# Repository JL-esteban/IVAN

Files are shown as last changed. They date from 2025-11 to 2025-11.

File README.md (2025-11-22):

Proyecto hecho por las siguientes personas:
- Jose Esteban Lopez Montoya
- Alejandro Rodriguez Cortès
- Duberney Campo Tabares
- Felipe Ramirez Satizabal

En este github mostramos las conexiones, codigos tanto en arduino como en ros2, tambien simulación en RViz, que nos llevo a fformular este proyecto?, a quien no le gustaria controlar algo con solo el mover de sus manos?, que sea algo entretenido a la hora de sus terapias de recuperacion?, que las personas lo puedan usar tanto a la hora de su terapia como un juguete.

Así que comenzamos, tenemos de la siguiente fora su conexión y la cantidad de objetos,componentes,baterias y microchips que usamos.

Vamos a comenzar con el principal, la mano, la mano es aquella que va a ser de control con los movimientos de su muñeca, tu te preguntaras, como?, muy sencillo hay un modulo que se llama BMI160 el cual es un giroscopio y acelerometro, este modulo se programo para que soltara las coordenadas X Y, asi convertimos con el acelerometro que mande las posiciones como si fuera un mando,  no sabes que hace un mando?, te lo explico:

El mando tiene una serie de nombres los cuales las computadoras detectan como por ejemplo cada palanca, movimiento o boton por un axis, en nuestro caso es un R3 de un mando (es la palanca de la izquierda) esta palanca tiene dos axis los cuales son axis0 y axis1, el axis0 son los movimientos de izquierda y derecha, el axis1 son los movimientos de arriba y abajo, estos sueltan unos numeros los cuales el computador traduce para generar un movimiento a un personaje.

Teniendo eso en mente se supo que con las coordenadas de la mano y su giro podiamos hacer un joystick, el que lee eso es un Arduino UNO, el cual obtiene los datos y se los manda a el computador.

Ahora el computador con los datos del BMI160 ya como un joystick mandara la señal atravez de wifi al microchip del semisumergible que esta en el agua para poder moverse.

Ahora te explicare que tiene el semisumergible, que los autores de este repositorio lo llamaron como IVAN,IVAN tiene un ESP32, el cual resive los datos del computador atravez del wifi que son las direcciones dadas por el joystick(BMI160), este ESP32 le mandara la señal a un puente h, el cual es un tb6612fng, y este segun las direcciones dadas comenzara a mandar el voltaje a las salidas de A0 y A1 que son las salidas del primer motor y B0 B1 que son las salidas del segundo motor, todos los gnds de esta mismas estan conectadas entre ellas, y asi este se desplazaria por el agua.

No nos olvidemos de lo mas importante ¿conque alimentamos a IVAN?, IVAN tiene dos tipos de alimentación interna, una que es solo para el ESP32 y el otro el cual es solo para los motores, para alimentar el ESP32 se utilizaron 3 paquetes de pilas AA y esta salida de voltaje que dan 9V entran a un regulador de voltaje creado (que aqui se pasara la kicad) para que asi entren 9V y salgan 5V un buen voltaje con un buen amperaje que salen de las pilas para mantener prendido el ESP32 por un largo rato aproximadamente 30-40min, el tb6612fng  tiene dos pines uno llamado VCC y otro VM el VCC es aquel que resive entre 3.3V a 5V, los autores del proyecto alimentaron a 5V el tb6612fng y el VM a una bateria de 7.4V 1500mA

-------------------------------------------------------------------------------------------------------------------------------------------
EL CODIGO, LO IMPORTANTE QUE NECESITAS SABER
-------------------------------------------------------------------------------------------------------------------------------------------

  el que se llama Codigo_BMI160 es aquel codigo que conectaras el BMI160 con el ARDUINO UNO, a continuaciòn te explico como conectarlo:

  El BMI160 de la placa que yo te paso es realmente de 4 pines que es VCC,GND,SDA,SCL
, esos se pondran de la siguiente forma con el ARDUINO UNO, y es:
ESP32             |ARDUINO UNO
VCC --------------->5V
GND---------------->GND
SCL----------------->A5
SDA----------------->A4

con esas conexiones y el codigo de arduino que se otorgo te debe comenzar a mostrar coordenadas en la terminal.

Luego las conexiones de el ESP32 son de la siguiente forma:

Tb6612fng           |  ESP32
AIN1 ----------------> 25;
AIN2 ----------------> 26;
PWMA ----------------> 27;
BIN1 ----------------> 32;
BIN2 ----------------> 33;
PWMB ----------------> 14;
STBY ----------------> 12;

lo que es VM y VCC fue explicado anteriormente, y los puntos A0.A1.B0.B1 son los puntos de los motores A y B, que tipo de motores usamos?, usamos motores Hélice submarina cepillada BM70.

-----------------------------------------------------------------------------------------------------------------------------------------
una vez que has tenido esto vamos ha abrir el RVizte 
#iremos a la carpeta de ros2_ws
cd ~/ros2_ws

#cada vez que hagas un cambio o abras por primera vez una terminal en ubuntu debes poner el siguiente com  ando es ley  
colcon build --packages-select robot_boat

#cargamos el entorno
source install/setup.bash

#y ejecuta para verlo en rviz
ros2 launch robot_boat display.launch.py 

------------------------------------------------------------------------------------------------------------------------------------------
Ahora para cargar los codigos hay que hacerse de la siguiente manera
Vas al archivo de "AVANCE2" que esta en el principio del GitHub y abres dos terminales y ejecutas los siguientes comandos
# Terminal 1 - Lector BMI
source /opt/ros/humble/setup.bash
python3 lector_bmi160.py --ros-args -p serial_port:=/dev/ttyUSB0

# Terminal 2 - Control barco (después de que Terminal 1 funcione)
source /opt/ros/humble/setup.bash
python3 bmi_to_boat_control.py --ros-args -p esp32_ip:=192.168.4.1





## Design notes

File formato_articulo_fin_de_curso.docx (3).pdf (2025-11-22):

Avances sobre implementación de un robot acuático controlado por movimientos de la muñeca para la estimulación de la motricidad fina en Colombia. [MK06],

# Artículo de investigación como proyecto fin de curso

Research paper as a course end project

Alejandro Rodríguez Cortés
alejandro_rod@uao.edu.co
Duberney Campo Tabares
duberney.campo@uao.edu.co

Felipe Ramírez Satizabal
felipe.ramirez@uao.edu.co
José Esteban López
jose_esteban.lopez@uao.edu.co

Universidad Autónoma de Occidente, Facultad de Ingeniería, Programa de Ingeniería Mecatrónica (1) Universidad Autónoma de Occidente, Facultad de Ingeniería, Programa de Ingeniería Mecatrónica (2) Universidad Autónoma de Occidente, Facultad de Ingeniería, Programa de Ingeniería Mecatrónica (3) Universidad Autónoma de Occidente, Facultad de Ingeniería, Programa de Ingeniería Mecatrónica (4)

Resumen
Este informe presenta el análisis y búsqueda exhaustiva de fuentes de información para llevar a cabo nuestro proyecto de Robótica que está en búsqueda de la mejoría en el sector médico enfocándonos en el tema de la estimulación de la motricidad fina en Colombia.

La motricidad fina, y en particular la movilidad de la muñeca es determinante para el desarrollo de la autonomía funcional en la primera infancia e infancia, y para la recuperación de pacientes con limitaciones neurológicas y musculo esqueléticas. Sin embargo, los métodos tradicionales de estimulación y rehabilitación de la muñeca suelen apoyarse en ejercicios repetitivos y poco motivadores, lo que reduce la adherencia y limita el progreso de recuperación de la coordinación, fuerza y precisión.

La robótica ha demostrado ser un recurso innovador para estimular el movimiento y aumentar la participación de los usuarios. En este marco, el uso de un robot acuático controlado directamente por los movimientos de la muñeca representa una alternativa atractiva y novedosa. Con este enfoque, la persona no se sumergirá en el agua, en cambio manipulará al robot desde el exterior al mover la muñeca, el robot en este caso es un barco o objeto semisumergible que responde al movimiento de la muñeca desplazándose en el agua. Esta dinámica convierte la práctica en una experiencia lúdica y atractiva, que permite entrenar y evaluar la motricidad fina de la articulación.

En Colombia, pese a los avances en robótica educativa y en proyectos de rehabilitación, no se han implementado sistemas que integren la robótica acuática con el control directo a través de la muñeca. Esta ausencia tecnológica limita las posibilidades de contar con herramientas accesibles que integren la estimulación motora, la retroalimentación inmediata y la motivación lúdica. Como consecuencia, tanto niños en edad escolar como pacientes en procesos de rehabilitación continúan dependiendo principalmente de métodos tradicionales, los cuales, aunque han demostrado un grado de efectividad, no siempre garantizan un progreso sostenido ni permiten una evaluación objetiva del desempeño motor.

Palabras Clave: Motricidad fina, robótica, estimulación

Abstract
This report presents the analysis and exhaustive search for sources of information to carry out our Robotics project, which seeks to improve the medical sector by focusing on the stimulation of fine motor skills in Colombia.

Fine motor skills, and in particular wrist mobility, are crucial for the development of functional autonomy in early childhood and for the recovery of patients with neurological and musculoskeletal limitations. However, traditional methods of wrist stimulation and rehabilitation often rely on repetitive and unmotivating exercises, which reduce adherence and limit progress in recovering coordination, strength, and precision.

Autor 1, Autor 2...& Autor N. [(año)]

Robotics has proven to be an innovative resource for stimulating movement and increasing user participation. In this context, the use of an aquatic robot controlled directly by wrist movements represents an attractive and novel alternative. With this approach, the person will not be submerged in water, but will instead manipulate the robot from the outside by moving their wrist. In this case, the robot is a boat or semi-submersible object that responds to the movement of the wrist by moving through the water. This dynamic makes the practice a fun and engaging experience, allowing for the training and evaluation of fine motor skills in the joint.

In Colombia, despite advances in educational robotics and rehabilitation projects, no systems have been implemented that integrate aquatic robotics with direct control via the wrist. This technological gap limits the availability of accessible tools that integrate motor stimulation, immediate feedback, and playful motivation. As a result, both school-age children and patients undergoing rehabilitation continue to rely primarily on traditional methods, which, although they have proven to be effective to a certain degree, do not always guarantee sustained progress or allow for an objective assessment of motor performance.

Keywords: Fine motor skills, robotics, stimulation

### 1. INTRODUCCIÓN

En el siguiente documento vamos a abordar los temas relacionados con la motricidad fina, con un enfoque en la movilidad de la muñeca, teniendo en cuenta los métodos de rehabilitación actuales que son repetitivos y poco motivadores lo cual limita el progreso en la recuperación de coordinación, fuerza y precisión.
El cómo se pueden solucionar ciertos problemas de esta área y como desde la robótica vamos a aportar hacia esta misma, la cual tiene pocas investigaciones acerca del uso de robótica de forma directa en el paciente sin necesidad de que este arme algún tipo de robot. Sino que él sea el que controle el robot a través de los movimientos que necesite hacer en su terapia.
La robótica ha mostrado un gran potencial en este campo, al ofrecer experiencias más dinámicas y efectivas en la estimulación motora. Sin embargo, la mayoría de las investigaciones existentes se centran en sistemas complejos o de alto costo, sin explorar alternativas accesibles que integren la motivación lúdica con la terapia. En Colombia, no se han desarrollado propuestas que utilicen robótica acuática controlada directamente por la muñeca, lo que abre un espacio de innovación.
En este contexto, la presente investigación propone un enfoque novedoso en el que el paciente no construye el robot, sino que lo controla a través de los movimientos requeridos en su terapia. De esta manera, se busca integrar la estimulación motora, la retroalimentación inmediata y la motivación lúdica, aportando al estado actual de la ciencia y a la comprensión del problema desde una perspectiva terapéutica y educativa.

### 2. MATERIALES Y MÉTODOS/METODOLOGÍA

Diseño Conceptual y Selección de Componentes
Iniciaremos investigando los ejercicios de rehabilitación para identificar los movimientos clave de la muñeca que controlarán el vehículo. Con base en esto, se seleccionará el sensor y microcontrolador idóneos para capturar dichos movimientos, junto con los motores y propulsores adecuados para el entorno acuático. Finalmente, se elaborará una lista detallada de todos los componentes de hardware necesarios y las herramientas de software a utilizar.

Desarrollo del Hardware y Software
Se enfoca en la construcción física del prototipo, montando los motores y sellando la electrónica en una caja hermética, mientras que en paralelo se programará el firmware para traducir los datos del sensor inercial de la muñeca en comandos de control que transmitidos de forma inalámbrica gobiernen la velocidad y dirección de los motores del vehículo acuático. Se construirá el prototipo físico, montando los motores y sellando la electrónica. Paralelamente, se programará el firmware para traducir los datos del sensor inercial de la muñeca en comandos de control que se transmitirán de forma inalámbrica para gobernar la velocidad y dirección del vehículo.

Para el control del robot, se utilizará un sistema embebido con Linux para aprovechar su flexibilidad en la programación y el uso de librerías avanzadas. Esto facilitará la implementación de algoritmos de filtrado (como un Filtro de Kalman) para reducir el ruido del sensor, lo cual es crucial para abordar los riesgos de control y programación .
Para mitigar los riesgos de integración de sistemas , el desarrollo se hará de manera modular. Primero se validará el funcionamiento de cada componente por separado y luego se integrarán progresivamente para asegurar una comunicación y un control fluidos y precisos. Este enfoque minimiza los problemas de compatibilidad y comunicación entre los distintos subsistemas del robot.

Diagramas de conexion y simulaciones

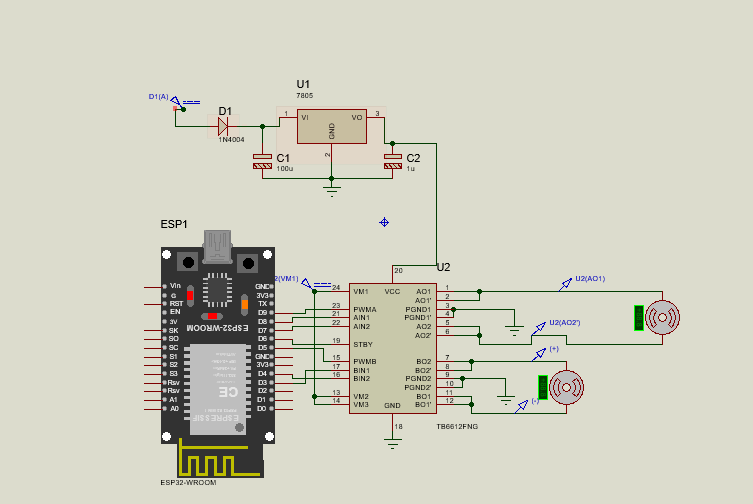
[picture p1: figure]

Imagen #1. Esquema interno de IVAN_Bote

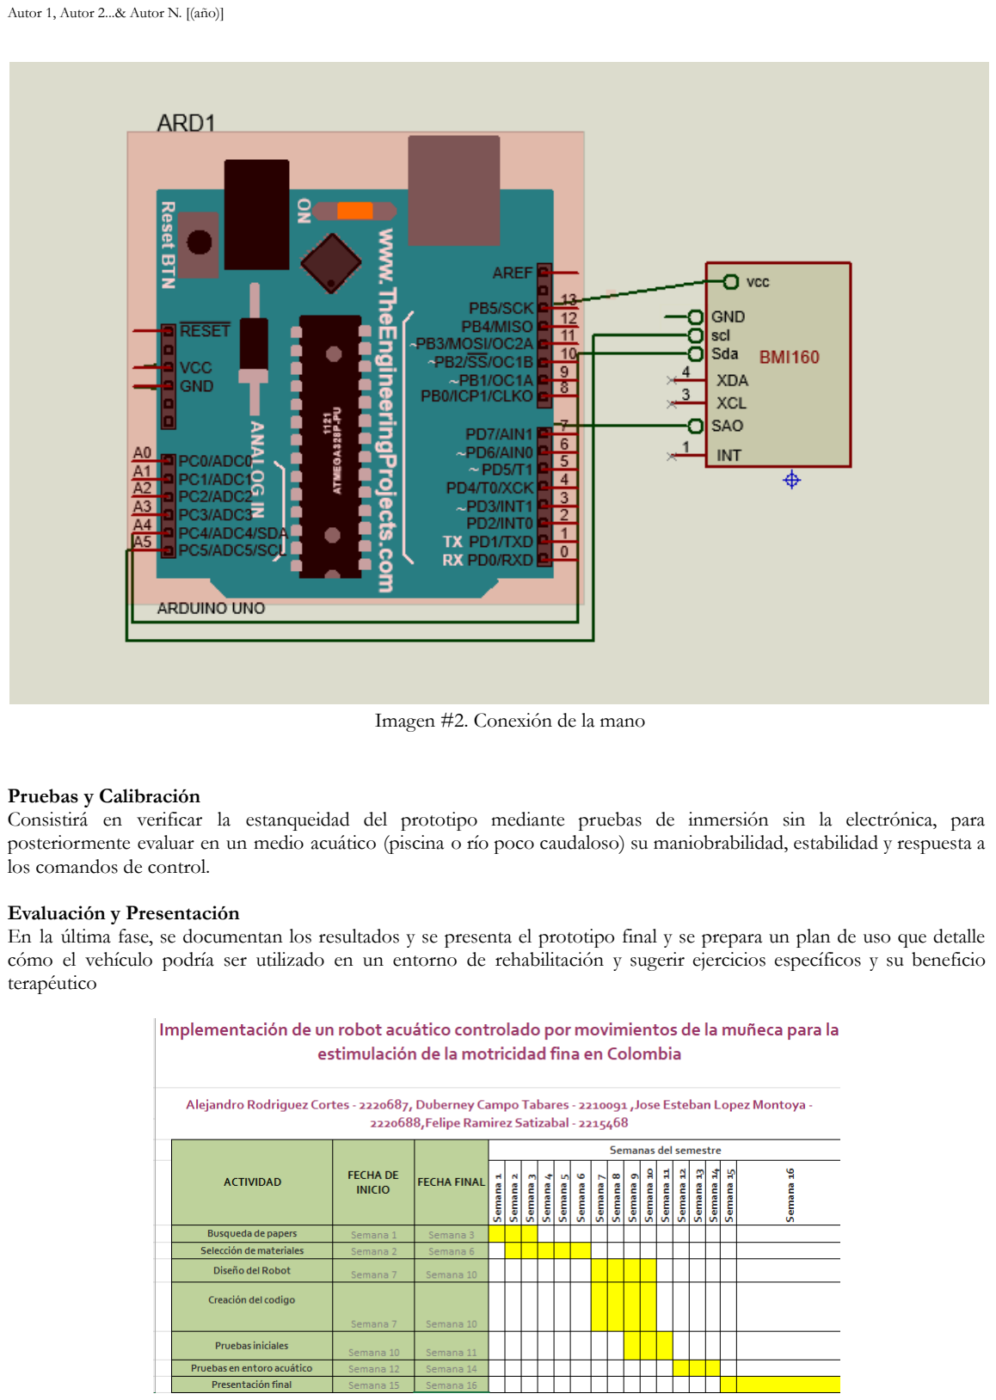
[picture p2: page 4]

Imagen #2. Conexión de la mano

Pruebas y Calibración
Consistirá en verificar la estanqueidad del prototipo mediante pruebas de inmersión sin la electrónica, para posteriormente evaluar en un medio acuático (piscina o río poco caudaloso) su maniobrabilidad, estabilidad y respuesta a los comandos de control.

Evaluación y Presentación
En la última fase, se documentan los resultados y se presenta el prototipo final y se prepara un plan de uso que detalle cómo el vehículo podría ser utilizado en un entorno de rehabilitación y sugerir ejercicios específicos y su beneficio terapéutico

Tabla #1. Elaboración propia

Tabla 1. Elaboración propia diagrama de gantt [8]

Se usará un microchip el cual con un sensor qué detecte el movimiento de la mano qué para ese tipo de casos un acelerómetro y giroscopio qué serian la mejor elección para esta tarea, se transmitirá una señal con un radio de 100m a la redonda y un receptor de la señal mandada, con una fuente de voltaje con 1500mAh y 11.1v, con un convertidor dc/dc se bajara el voltaje de 11.1v a 8.4v para un puente h y así poder alimentar los motores, se usarán unos botones para apagar tanto el mecanismo de la mano como el robot qué andará en el agua, se usara otro botón para qué el robot quede medio cuerpo sumergido utilizando el principio del submarino qué es absorber agua en un tanque haciendo qué se sumerja en el agua

Los componentes qué se va a usar en el proyecto son:

objeto | cantidad | dólar | peso colombiano | link de compra
Conector de cable de alambre rápido de 2A, 250 V, 2 pines, 3 pines | 20 | | $ 8.000 | averigua duberney
eBoot 20 AWG JST Cables y conectores para lámparas LED | 4 | | $ 8.000 | averigua duberney
bmi160 | 1 | | $ 22.990 | Bmi160 Acelerómetro Y Giroscopio 6dof Gybmi160 | Cuotas sin interés (https://articulo.mercadolibre.com.co/MCO-637322661-bmi160-acelerometro-y-giroscopio-6dof-gybmi160-_JM)
Batería Lipo Turnigy 1000mah 3s 20c | 1 | | $ 82.000 | Batería Lipo Turnigy 1000mah 3s 20c | Cuotas sin interés (https://articulo.mercadolibre.com.co/MCO-1559039399-bateria-lipo-turnigy-1000mah-3s-20c-_JM)
Teyleten Robot TB6612FNG Dual DC motor paso a paso módulo controlador 1.2A pico 3.2A | 1 | $ 7,81 | $ 31.445 | ENLACE (https://www.amazon.com/-/es/Teyleten-TB6612FNG-m%C3%B3dulo-controlador-paquete/dp/B08J3S6G2N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)
LEADTOPS Cable de extensión LED RGB de 100 pies | 10m | | $ 34.000 | Cable Rgb 4 Hilos Para Extensiones De Cinta Led X (https://articulo.mercadolibre.com.co/MCO-592184567-cable-rgb-4-hilos-para-extensiones-de-cinta-led-x-10-metros-_JM)

| | | | 10 Metros | Cuotas sin interés (https://articulo.mercadolibre.com.co/MCO-592184567-cable-rgb-4-hilos-para-extensiones-de-cinta-led-x-10-metros-_JM)
Qidoe 5 interruptores basculantes redondos impermeables | 1 | | $ 1.900 | averigua duberney
2S Lipo - Hélice submarina cepillada BM70 de 8.4 V 22 W, sellado, impermeable, para bricolaje, juguete, ROV | 2 | $ 16,98 | $ 68.367 | Enlace
Convertidor DC-dc XL4015 5a | 1 | | $ 18.500 | averigua duberney
módulo ASK 433 MHz 100 metros transmisor RF STX882 y antena receptor SRX882 | 1 | | $ 4.000
PETG | | | $ 85.000
Módulo ESP32-Cam-MB con cámara Ov2640 ESP de 32 Mb | 1 | | $ 44.6 90 | Módulo ESP32-Cam-M B con cámara Ov2640 ESP de 32 Mb | Cuotas sin interés (https://www.mercadolibre.com.co/modulo-esp32-cam-mb-con-camara-ov2640-esp-de-32-mb/p/MCO36063720)
| | COMPLETO | $ 408.892
por persona | $ 102.223 | dólar hoy | 4026,3
nombres | Dinero que dio | mercado libre | $ 138.260
Alejandro | $ 170.400 | Bateria | $ 84.000
Duberney | $ 208.800 | ALI EXPRESS | $ 16.000
Esteban | $ 161.000 | Amazon | $ 172.078
Felipe | $ 109.000 | Centro | $ 67.000 | Falta

IMPREVISTOS | $ 160.446 | total de web | $ 477.338
total de personas que dio plata | $ 649.200

Tabla #2. Componentes y presupuesto del proyecto

### 3. RESULTADOS Y DISCUSIÓN

El desarrollo de este proyecto inició con un análisis riguroso de literatura y la recopilación de diversas perspectivas orientadas a justificar la pertinencia de abordar la motricidad fina mediante herramientas robóticas. La revisión incluyó trabajos relacionados con parálisis cerebral, terapias motoras y tecnologías aplicadas a la rehabilitación, los cuales permitieron comprender la relevancia clínica y pedagógica del entrenamiento de la motricidad fina en población infantil [1]–[4]. Asimismo, investigaciones recientes sobre sistemas robóticos aplicados a procesos terapéuticos evidencian que las plataformas interactivas y los entornos asistidos por tecnología pueden mejorar significativamente la participación y el desempeño motor de los usuarios [5]–[9]. A partir de estas fuentes se identificó una problemática central: los ejercicios tradicionales de motricidad fina suelen ser repetitivos y poco motivadores, especialmente para niños con dificultades motoras, lo cual reduce la adherencia y la efectividad del tratamiento [6], [7]. Esta observación permitió establecer la necesidad de una alternativa innovadora que integrara estimulación, motivación y control motor mediante un dispositivo robótico accesible y atractivo.

Con base en este análisis se planteó la propuesta de desarrollar un robot acuático controlado mediante los movimientos de la muñeca, empleando un sensor inercial para captar los gestos del usuario y transferirlos directamente al desplazamiento del robot en el agua. La literatura relacionada con sistemas robóticos en contextos clínicos y de interacción háptica–visual brindó fundamentos sobre el uso de dispositivos lúdicos como herramienta terapéutica, así como sobre el impacto positivo de la interacción física y el feedback inmediato en la recuperación motora [5], [9], [10], [14].

Posteriormente se realizó una revisión de trabajos similares y de propuestas tecnológicas aplicadas a entornos acuáticos, lo que permitió comprender el estado del arte y definir una ruta de desarrollo adecuada [12], [13]. Con esta base se seleccionaron los componentes esenciales del sistema: motores impermeables para la movilidad en el agua, un sensor BMI160 para captar los movimientos de la muñeca y microcontroladores encargados del procesamiento y la comunicación. Aunque se emplearon otros elementos complementarios (reguladores, baterías y partes estructurales), estos componentes constituían la base funcional del sistema de control.

Inicialmente se contempló el uso de un sistema de transmisión radial para enviar desde un emisor en la muñeca las lecturas del BMI160 hacia un receptor ubicado en el robot. Sin embargo, durante las fases preliminares se identificaron limitaciones importantes en estabilidad y alcance de la señal, lo cual dificultaba su integración fluida durante la terapia. Este tipo de limitaciones en la comunicación es consistente con lo documentado en la literatura sobre diseño de robots móviles y procesos cooperativos entre dispositivos [11]. Debido a estos inconvenientes, se decidió migrar hacia un esquema más robusto basado en la conectividad WiFi del ESP32, mientras que el BMI160 se integró a un Arduino Uno para la captura de datos. Esta combinación permitió obtener un control más estable y una respuesta más suave, logrando que los movimientos de la muñeca se reflejaran de manera directa y precisa en el desplazamiento del robot.

El diseño físico del robot, su integración electrónica y las pruebas de funcionamiento representaron una de las etapas más enriquecedoras del proyecto. Controlar un robot acuático mediante los movimientos de la muñeca ofreció una experiencia particularmente innovadora, en contraste con los dispositivos tradicionales que emplean controles manuales convencionales. Además, el diseño buscó ser amigable y atractivo para niños con dificultades motoras, siguiendo recomendaciones de estudios previos que resaltan el valor del componente lúdico para mejorar la disposición del usuario en actividades terapéuticas [5]–[7]. Esta característica resultó fundamental: en las pruebas iniciales los usuarios manifestaban tal nivel de inmersión y disfrute que, en muchos casos, olvidaban que realizaban ejercicios de terapia, confirmando el potencial motivacional señalado en la literatura [6], [9], [14].

Durante el proceso de simulación se lograron avances importantes, aunque también se enfrentaron desafíos significativos. El entorno RViz permitió una visualización correcta del modelo y facilitó la comprensión espacial del robot dentro del entorno virtual. Sin embargo, en Gazebo se presentaron múltiples dificultades debido al alto peso computacional de los archivos STL, lo que provocaba bloqueos frecuentes y fallos completos del sistema. Este tipo de limitaciones es común en simulaciones complejas de robots con geometrías detalladas, especialmente cuando el hardware disponible es limitado [9], [13]. La única manera de obtener una simulación funcional fue reduciendo la geometría a modelos extremadamente simples, lo que se alejaba considerablemente del diseño real, pero aun así permitió validar conceptos fundamentales sobre optimización en ROS2.

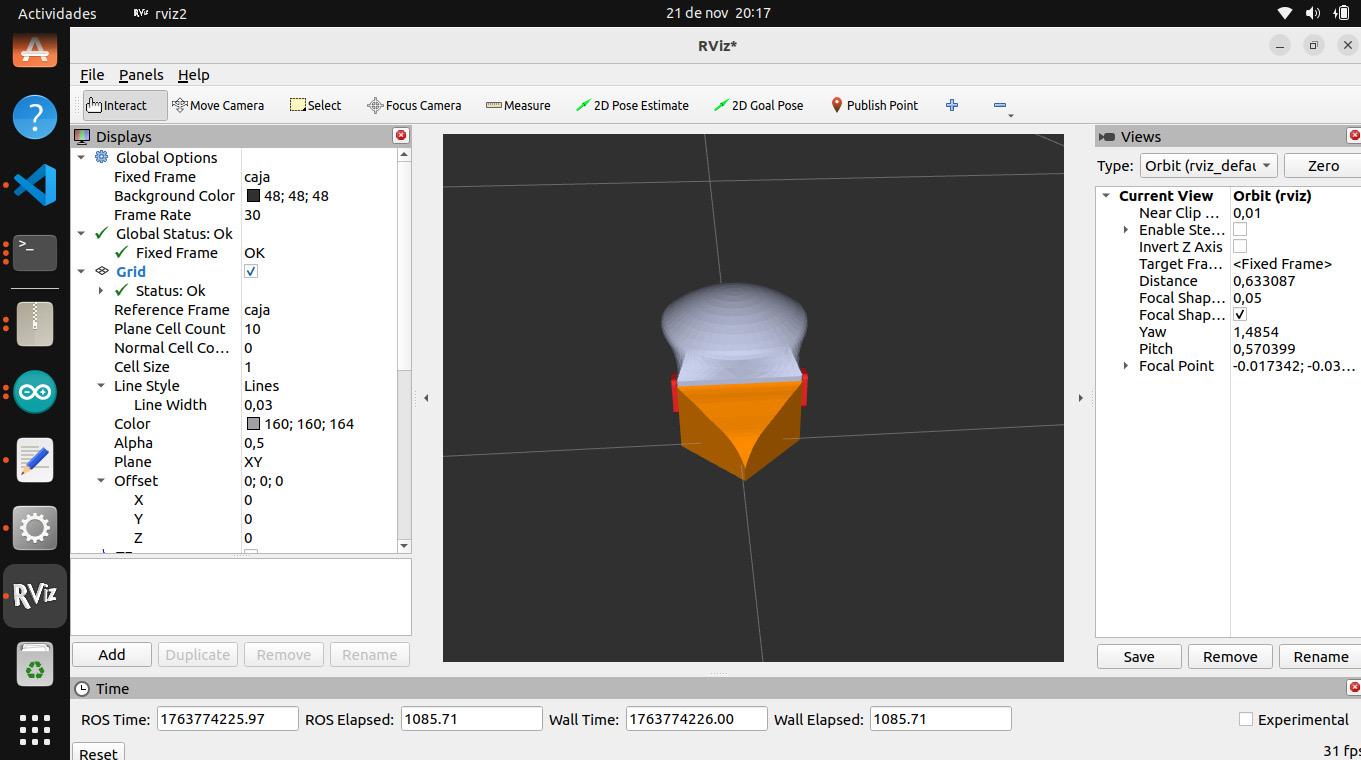
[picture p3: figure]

Imagen #3. Rviz de nuestro robo- elaboración propia

El uso de ROS2 representó un aprendizaje profundo, al requerir la instalación y manejo de un sistema operativo específico, la comprensión de la arquitectura basada en nodos y la integración de distintos paquetes para visualización, simulación y comunicación. Este proceso amplió de manera notable nuestra comprensión de la robótica moderna y de los ecosistemas distribuidos que sustentan el desarrollo de sistemas autónomos en la actualidad [9], [11], [14].

Finalmente, el proyecto resultó altamente enriquecedor desde los ámbitos técnico, terapéutico y humano. Su implementación a mayor escala podría transformar la manera en que se desarrollan las terapias de motricidad fina, aportando una herramienta innovadora, motivante y eficaz, coincidiendo con las tendencias descritas en la literatura sobre rehabilitación asistida por robots [5], [9], [10], [13]. El único inconveniente real durante la implementación física fue el consumo energético: las pilas alcalinas utilizadas para alimentar el ESP32 se descargaban rápidamente, reduciendo el tiempo de operación y exigiendo reemplazos frecuentes. Este aspecto constituye una oportunidad clara de mejora para futuras versiones, mediante el uso de baterías recargables de mayor capacidad o sistemas de gestión energética más eficientes. En conjunto, el proyecto demuestra cómo la robótica puede integrarse de forma creativa y funcional en procesos terapéuticos, ofreciendo experiencias más atractivas, inmersivas y efectivas para los usuarios [5]–[9], [14].

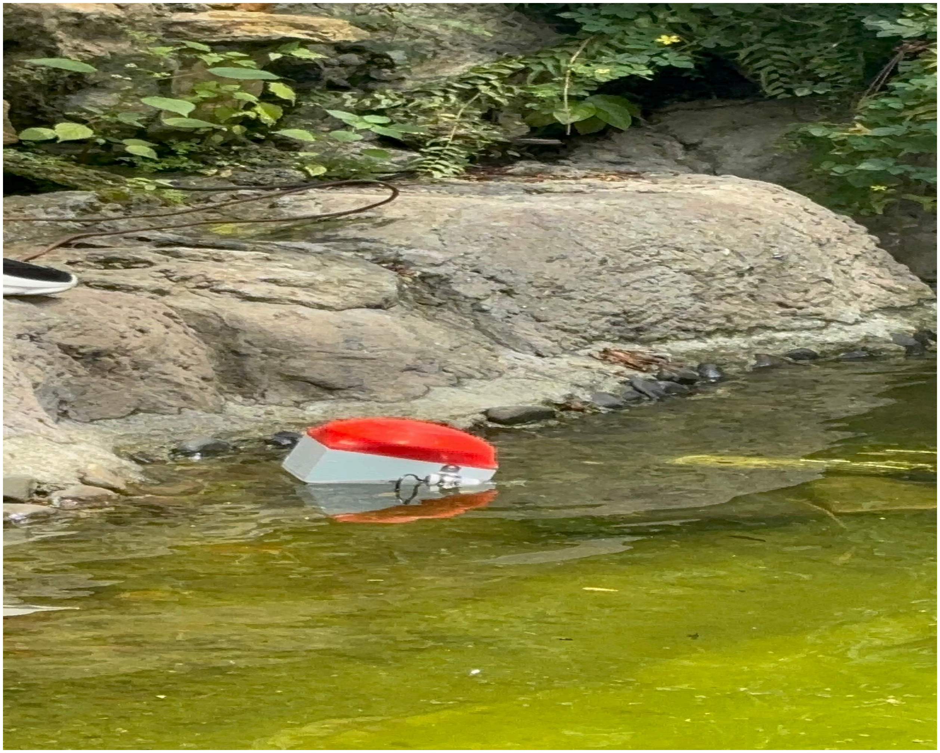
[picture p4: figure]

Imagen #4. IVAN en su primera prueba en el lago de la universidad

### 4. CONCLUSIONES

El proyecto demostró que la integración de tecnologías robóticas con enfoques terapéuticos puede mejorar significativamente los procesos de rehabilitación de la motricidad fina, especialmente en población infantil. A lo largo de su desarrollo se comprobó que el empleo de un robot acuático controlado mediante los movimientos de la muñeca no solo introduce un componente innovador, sino que también incrementa la motivación, la participación activa y la adherencia del usuario a las actividades terapéuticas. La combinación entre el sensor inercial, el control mediante ESP32 y el diseño amigable del robot permitió transformar ejercicios tradicionalmente repetitivos en experiencias lúdicas y dinámicas, lo cual constituye un aporte valioso para la fisioterapia y la rehabilitación motora.

En conjunto, los resultados del proyecto evidencian que la robótica, cuando se diseña con enfoque terapéutico y centrado en el usuario, puede convertirse en una herramienta altamente funcional, motivante y con potencial de impacto clínico. Esta iniciativa abre la puerta a nuevas investigaciones y mejoras, orientadas a robustecer el sistema, ampliar su autonomía y explorar otras aplicaciones en rehabilitación motora, posicionándose como un aporte significativo al campo de la tecnología para la salud.

REFERENCIAS

[1] S. Ccalla Auqui, Abordajes en parálisis cerebral infantil, Universidad Peruana Cayetano Heredia, 2023. [En
línea]. | Disponible | en:
https://repositorio.upch.edu.pe/bitstream/handle/20.500.12866/17241/Abordajes_CcallaAuqui_Sara.pdf?sequence=1
[2] D. Harghel Macari, Parálisis cerebral en el marco del máster universitario de fisioterapia en pediatría. Eficacia de la Terapia Acuática sobre la función motora gruesa en niños con Parálisis Cerebral con GMFCS I-IV , Trabajo Fin de Máster, Universidad Internacional de Valencia, 20210 https://eugdspace.eug.es/bitstream/handle/20.500.13002/821/Terapia%20Acu%c3%a1tica%20en%20Par%c3%a1lisis%20Cerebral.pdf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. (https://eugdspace.eug.es/bitstream/handle/20.500.13002/821/Terapia%20Acu%c3%a1tica%20en%20Par%c3%a1lisis%20Cerebral.pdf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)
[3] Recursos de Fisioterapia, “Escala de Función Motora Gruesa (GMFM) – Explicación completa y detallada.” Disponible en:
https://recursosfisioterapia.com/cuestionario-de-funcion-motora-gruesa-gmfm/
[4] CanChild, “GMFCS – E & R © 2007 CanChild Centre for Childhood Disability Research. Clasificación de la Función Motora Gruesa Extendida y Revisada. Disponible en: https://neuropediatoolkit.org/wp-content/uploads/2024/03/GMFCS-ER_Translation-Spanish.pdf
[5] A. L. Guerrero Hernández, Ó. A. Vivas Albán y J. M. Sabater Navarro, “Sistema de rehabilitación de motricidad fina de miembro superior utilizando juegos serios,” Ingeniería y Desarrollo, vol. 41, n.º 1, Universidad del Norte, 2023.
https://rcientificas.uninorte.edu.co/index.php/ingenieria/article/view/14894/214421446371
[6] Comunicación breve, “Escalas de motricidad fina,” Revista de Neurología Pediátrica, 2023. https://revistasanitariadeinvestigacion.com/escalas-de-motricidad-fina-comunicacion-breve/?utm_source=
[7] J. N. Orobio Aguiño y J. M. Montaño Rodriguez, Fortalecimiento de las habilidades motrices finas a través de actividades lúdicas en niños y niñas de 3 a 5 años del Hogar Comunitario La Fortaleza, Municipio de San Andrés de Tumaco (Nariño), Trabajo de grado (Profesional), Universidad Nacional Abierta y a Distancia (UNAD), 17 de abril de 2025.. Disponible en: https://repository.unad.edu.co/handle/10596/67947
[8] Elaboración propia agosto 29, 2025. Duberney Campo, Alejandro Rodriguez, Esteban Lopez y Felipe Ramirez.
[9] R. Llamas-Ramos, Robotic systems for the physiotherapy treatment of cerebral palsy, International Journal of Environmental Research and Public Health, vol. 19, no. 9, 2022. . Disponible en: https://www.mdpi.com/1660-4601/19/9/5116?utm_source
[10] B. R. Brewer, S. K. McDowell y L. C. Worthen-Chaudhari, “Poststroke upper extremity rehabilitation: a review of robotic systems and clinical results,” Topics in Stroke Rehabilitation, vol. 14, no. 6, pp. 22–44, 2007.. Disponible en: https://pubmed.ncbi.nlm.nih.gov/18174114/
[11] R. C. Arkin, T. Balch y E. Nitz, “Communication of Behavioral State in Multi-Agent Retrieval Tasks,” Proceedings of IEEE International Conference on Robotics and Automation, 1995. doi: 10.1109/ROBOT.1995.1511216. Disponible en: https://ieeexplore.ieee.org/abstract/document/1511216
[12] Y. Li, H. Zhao, X. Chen y J. Zhang, “Development of a Water Surface Cleaning Robot: Design, Implementation, and Experiment,” Applied Sciences, vol. 12, no. 18, p. 9131, 2022. . Disponible en: https://www.mdpi.com/2076-3417/12/18/9131
[13] H. H. Lee, Y. J. Kim y S. K. Park, “Design and Development of a Rehabilitation Robot for Ankle Motricity Training,” Machines, vol. 9, no. 11, p. 254, 2021. Disponible en: https://www.mdpi.com/2075-1702/9/11/254
[14] L. B. Cortés, “Desarrollo de un entorno virtual para la rehabilitación motriz basado en interacciones háptico-visuales”, Revista Iberoamericana de Automática e Informática Industrial, vol. 9, no. 4, pp. '–' (año), Universidad Politécnica de Valencia. [En línea]. Disponible: https://polipapers.upv.es/index.php/RIAI/article/view/9043/9714

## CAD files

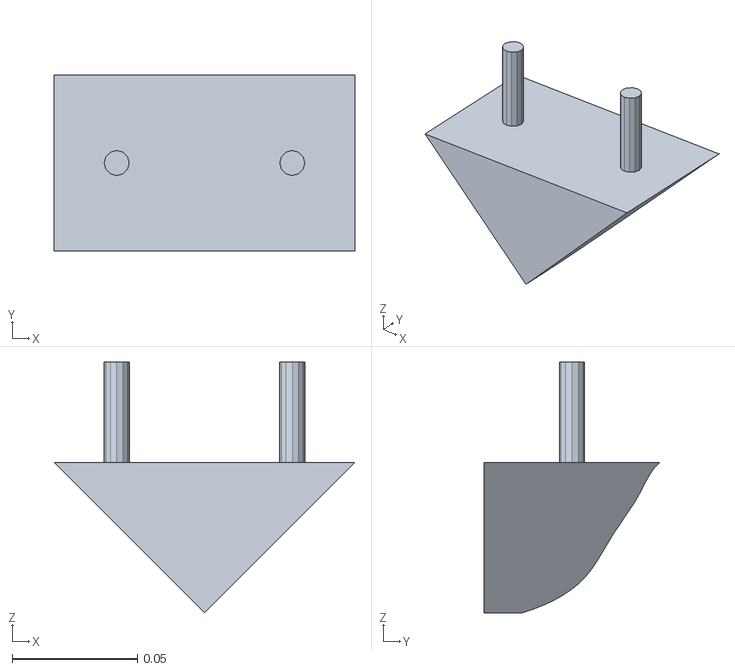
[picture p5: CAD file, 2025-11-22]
src/robot_boat/meshes/punta.STL
0.12 x 0.07 x 0.1

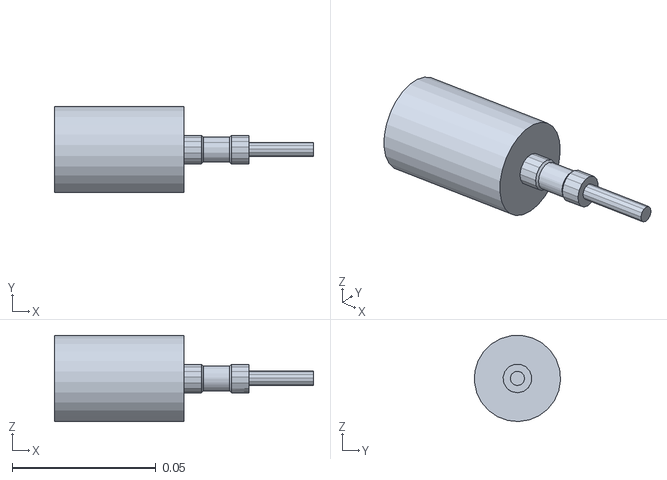
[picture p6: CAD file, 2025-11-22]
src/robot_boat_simple/robot_boat_simple/meshes/motor2.STL
0.09 x 0.0299 x 0.0299

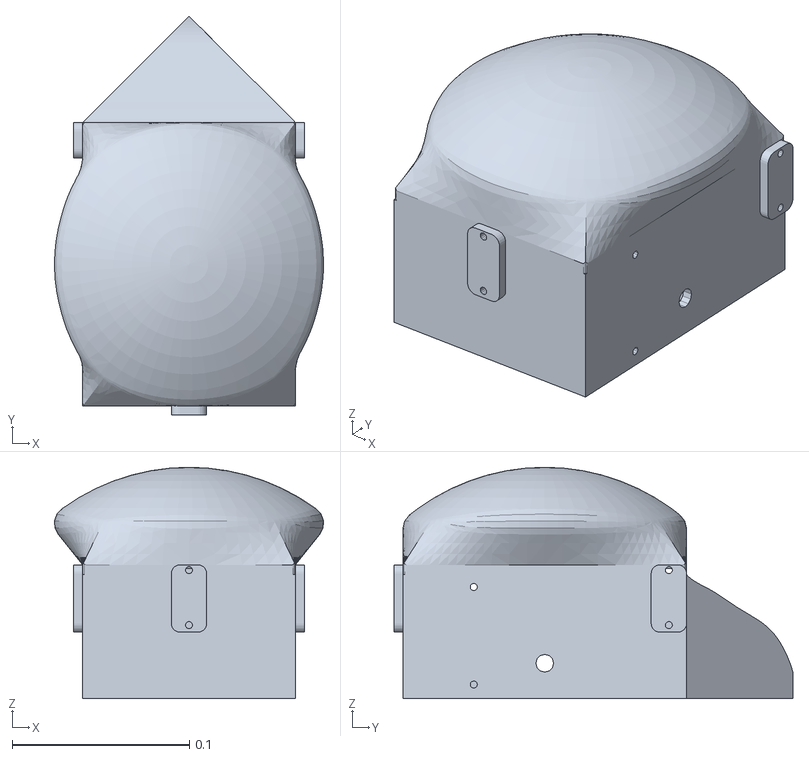
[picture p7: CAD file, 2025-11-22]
src/robot_boat_simple/robot_boat_simple/meshes/caja.STL
0.152 x 0.225 x 0.13

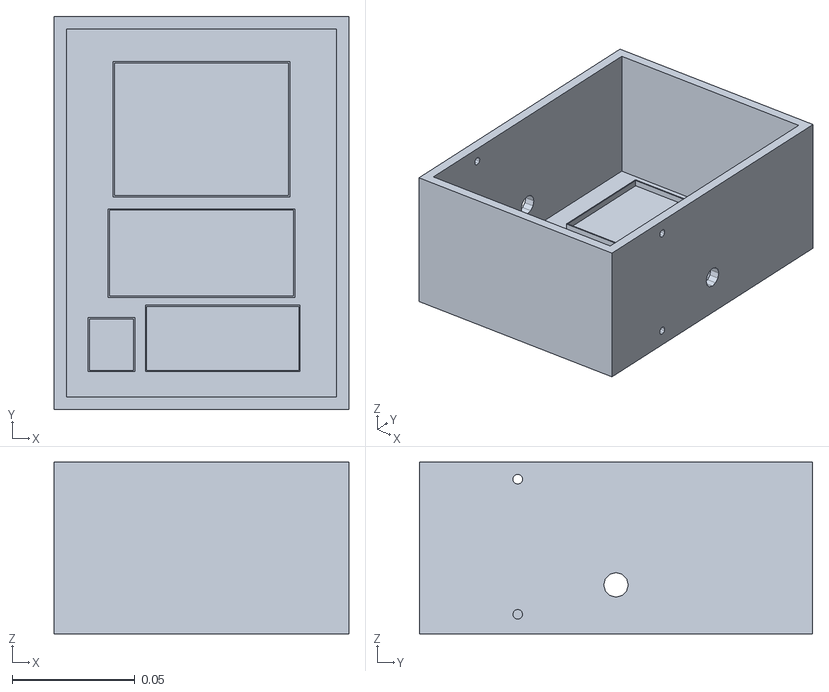
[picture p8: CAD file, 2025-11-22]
src/robot_boat/meshes/caja.STL
0.12 x 0.16 x 0.07

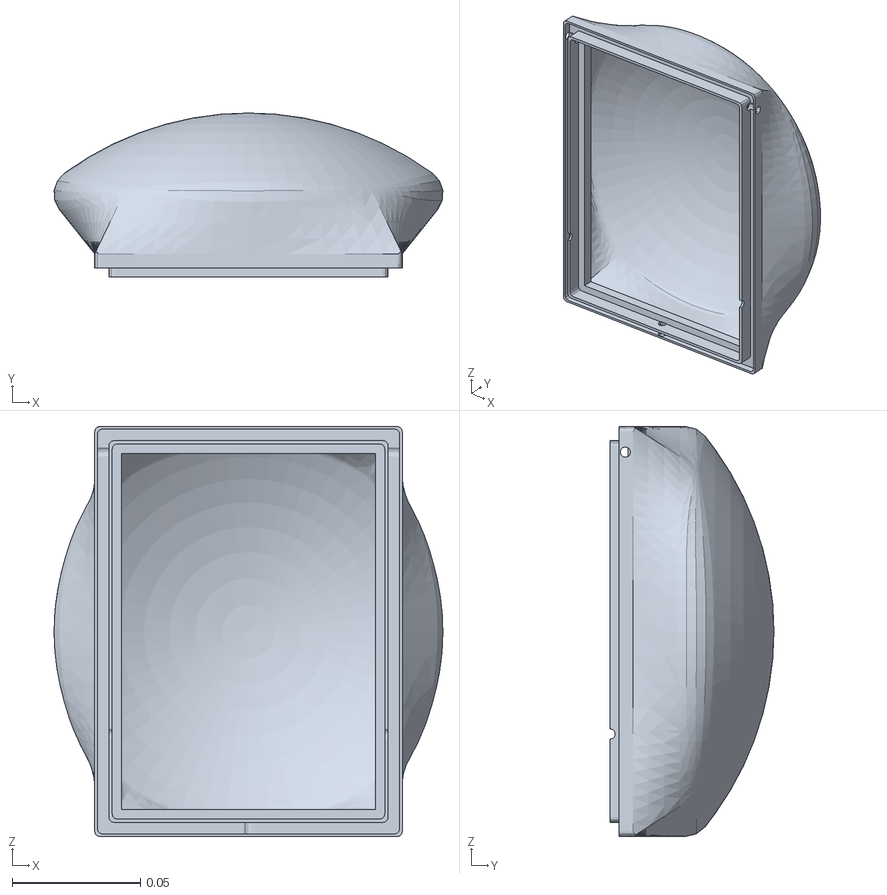
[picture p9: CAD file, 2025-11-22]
src/robot_boat/meshes/cabeza.STL
0.152 x 0.064 x 0.16

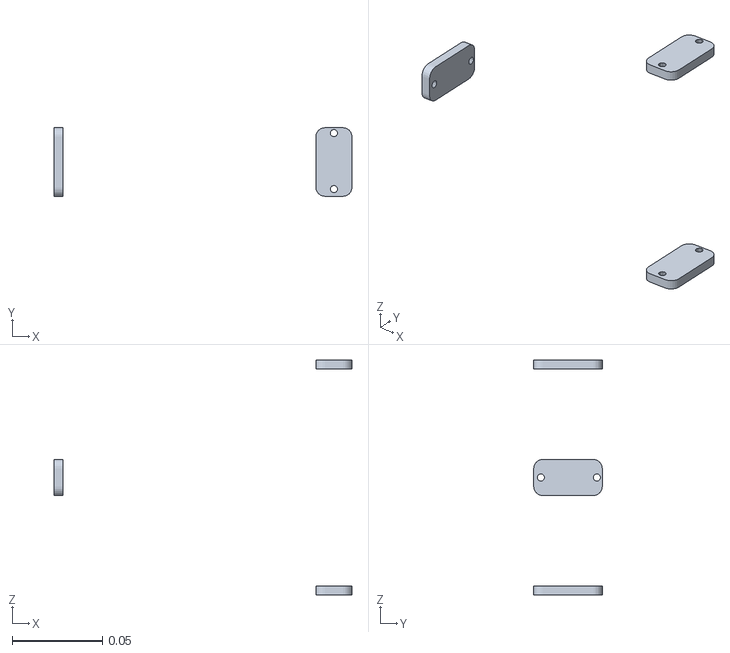
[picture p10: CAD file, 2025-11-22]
src/robot_boat/meshes/ganchos.STL
0.165 x 0.038 x 0.13

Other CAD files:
src/robot_boat/meshes/motor2.STL
src/robot_boat_simple/robot_boat_simple/meshes/motor1.STL
src/robot_boat/meshes/motor1.STL

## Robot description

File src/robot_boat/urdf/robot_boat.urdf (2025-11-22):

<?xml version="1.0" encoding="utf-8"?>
<robot name="robot_boat">

  <link name="caja">
    <inertial>
      <origin xyz="-0.00350655617226021 0.0057870557154398 0.100314646324909" rpy="0 0 0" />
      <mass value="0.315668074424316" />
      <inertia ixx="0.00106952247168509" ixy="-6.35663584540256E-08" ixz="4.48722793894617E-07" iyy="0.00147003359417461" iyz="1.732567854706E-06" izz="0.000700072373673693" />
    </inertial>
    <visual>
      <origin xyz="0 0 0" rpy="0 0 0" />
      <geometry>
        <mesh filename="package://robot_boat/meshes/caja.STL" />
      </geometry>
      <material name="azul_claro">
        <color rgba="0.792156862745098 0.819607843137255 0.933333333333333 1" />
      </material>
    </visual>
    <collision>
      <origin xyz="0 0 0" rpy="0 0 0" />
      <geometry>
        <mesh filename="package://robot_boat/meshes/caja.STL" />
      </geometry>
    </collision>
  </link>

  <link name="ganchos">
    <inertial>
      <origin xyz="-0.0508333333333334 -1.76145864720992E-05 -0.06" rpy="0 0 0" />
      <mass value="0.0107011061266654" />
      <inertia ixx="1.31036565577676E-06" ixy="1.52182167501141E-22" ixz="4.74293249589487E-24" iyy="3.76232518888044E-07" iyz="5.31604809467197E-23" izz="1.42091384800796E-06" />
    </inertial>
    <visual>
      <origin xyz="0 0 0" rpy="0 0 0" />
      <geometry>
        <mesh filename="package://robot_boat/meshes/ganchos.STL" />
      </geometry>
      <material name="rojo">
        <color rgba="1 0.168627450980392 0.168627450980392 1" />
      </material>
    </visual>
    <collision>
      <origin xyz="0 0 0" rpy="0 0 0" />
      <geometry>
        <mesh filename="package://robot_boat/meshes/ganchos.STL" />
      </geometry>
    </collision>
  </link>

  <joint name="ganchos" type="fixed">
    <origin xyz="0.056509 -0.03 0.039668" rpy="1.5708 0 1.5708" />
    <parent link="caja" />
    <child link="ganchos" />
    <axis xyz="0 0 0" />
  </joint>

  <link name="cabeza">
    <inertial>
      <origin xyz="-1.47210003906893E-05 0.0334212800408631 -1.71087868535286E-05" rpy="0 0 0" />
      <mass value="0.195566086436615" />
      <inertia ixx="0.000521416706885964" ixy="-3.28003379479109E-08" ixz="4.29670857435128E-08" iyy="0.000848517982242861" iyz="-6.74994053841756E-08" izz="0.000443795962264069" />
    </inertial>
    <visual>
      <origin xyz="0 0 0" rpy="0 0 0" />
      <geometry>
        <mesh filename="package://robot_boat/meshes/cabeza.STL" />
      </geometry>
      <material name="azul_claro">
        <color rgba="0.792156862745098 0.819607843137255 0.933333333333333 1" />
      </material>
    </visual>
    <collision>
      <origin xyz="0 0 0" rpy="0 0 0" />
      <geometry>
        <mesh filename="package://robot_boat/meshes/cabeza.STL" />
      </geometry>
    </collision>
  </link>

  <joint name="cabeza" type="fixed">
    <origin xyz="-0.07 0.01 -0.06" rpy="0 1.5707963267949 0" />
    <parent link="ganchos" />
    <child link="cabeza" />
    <axis xyz="0 0 0" />
  </joint>

  <link name="punta">
    <inertial>
      <origin xyz="3.27284758360044E-06 -0.00433760804571402 0.0273160015482659" rpy="0 0 0" />
      <mass value="0.0716405181094412" />
      <inertia ixx="5.44743781091978E-05" ixy="1.86774753169867E-09" ixz="6.76801340593279E-09" iyy="9.58237376978415E-05" iyz="-6.17934926455551E-06" izz="0.000101029420324114" />
    </inertial>
    <visual>
      <origin xyz="0 0 0" rpy="0 0 0" />
      <geometry>
        <mesh filename="package://robot_boat/meshes/punta.STL" />
      </geometry>
      <material name="naranja">
        <color rgba="1 0.549019607843137 0 1" />
      </material>
    </visual>
    <collision>
      <origin xyz="0 0 0" rpy="0 0 0" />
      <geometry>
        <mesh filename="package://robot_boat/meshes/punta.STL" />
      </geometry>
    </collision>
  </link>

  <joint name="punta" type="fixed">
    <origin xyz="-0.0034915 0.02 0.018168" rpy="1.5708 0 0" />
    <parent link="caja" />
    <child link="punta" />
    <axis xyz="0 0 0" />
  </joint>


  <link name="motor1">
    <inertial>
      <origin xyz="0.0248078639783107 0 0" rpy="0 0 0" />
      <mass value="0.0338272475621472" />
      <inertia ixx="3.59775886940148E-06" ixy="-8.70714672756417E-24" ixz="-9.65307491393635E-22" iyy="1.02720341448678E-05" iyz="0" izz="1.02720341448678E-05" />
    </inertial>
    <visual>
      <origin xyz="0 0 0" rpy="0 0 0" />
      <geometry>
        <mesh filename="package://robot_boat/meshes/motor1.STL" />
      </geometry>
      <material name="gris_claro">
        <color rgba="0.796078431372549 0.823529411764706 0.937254901960784 1" />
      </material>
    </visual>
    <collision>
      <origin xyz="90 0 0" rpy="0 0 0" />
      <geometry>
        <mesh filename="package://robot_boat/meshes/motor1.STL" />
      </geometry>
    </collision>
  </link>

  <joint name="motor1" type="continuous">
    <origin xyz="-0.04 -0.12 0.02" rpy="0 1.5708 0" />
    <parent link="caja" />
    <child link="motor1" />
    <axis xyz="1 0 0" />
    <limit effort="10.0" velocity="10.0" />
    <dynamics damping="0.1" friction="0.05" />
  </joint>


  <link name="motor2">
    <inertial>
      <origin xyz="0.0248078639783108 -6.93889390390723E-18 0" rpy="0 0 0" />
      <mass value="0.0338272475621472" />
      <inertia ixx="3.59775886940148E-06" ixy="3.03672443546408E-22" ixz="-1.21326837735656E-21" iyy="1.02720341448678E-05" iyz="0" izz="1.02720341448678E-05" />
    </inertial>
    <visual>
      <origin xyz="0 0 0" rpy="0 0 0" />
      <geometry>
        <mesh filename="package://robot_boat/meshes/motor2.STL" />
      </geometry>
      <material name="gris_claro">
        <color rgba="0.796078431372549 0.823529411764706 0.937254901960784 1" />
      </material>
    </visual>
    <collision>
      <origin xyz="0 0 0" rpy="0 0 0" />
      <geometry>
        <mesh filename="package://robot_boat/meshes/motor2.STL" />
      </geometry>
    </collision>
  </link>

  <joint name="motor2" type="continuous">
    <origin xyz="0.04 -0.12 0.02" rpy="0 1.5708 0" />
    <parent link="caja" />
    <child link="motor2" />
    <axis xyz="1 0 0" />
    <limit effort="10.0" velocity="10.0" />
    <dynamics damping="0.1" friction="0.05" />
  </joint>

  <gazebo reference="caja">
    <material>Gazebo/Blue</material>
    <kp>1000000.0</kp>
    <kd>100.0</kd>
  </gazebo>
  
  <gazebo reference="ganchos">
    <material>Gazebo/Red</material>
    <kp>1000000.0</kp>
    <kd>100.0</kd>
  </gazebo>
  
  <gazebo reference="cabeza">
    <material>Gazebo/Blue</material>
    <kp>1000000.0</kp>
    <kd>100.0</kd>
  </gazebo>
  
  <gazebo reference="punta">
    <material>Gazebo/Orange</material>
    <kp>1000000.0</kp>
    <kd>100.0</kd>
  </gazebo>
  
  <gazebo reference="motor1">
    <material>Gazebo/Grey</material>
    <kp>1000000.0</kp>
    <kd>100.0</kd>
  </gazebo>
  
  <gazebo reference="motor2">
    <material>Gazebo/Grey</material>
    <kp>1000000.0</kp>
    <kd>100.0</kd>
  </gazebo>

  <!-- Gazebo plugins -->
  <gazebo>
    <plugin name="gazebo_ros_control" filename="libgazebo_ros_control.so">
      <robot_namespace>/</robot_namespace>
    </plugin>
  </gazebo>

</robot>

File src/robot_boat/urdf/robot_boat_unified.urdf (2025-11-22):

<robot name="robot_boat">
  
  <!-- CUERPO PRINCIPAL (usando el STL de la caja) -->
  <link name="base">
    <inertial>
      <origin xyz="0 0 0.025" rpy="0 0 0" />
      <mass value="0.4" />
      <inertia ixx="0.001" ixy="0" ixz="0" iyy="0.001" iyz="0" izz="0.001" />
    </inertial>
    <visual>
      <geometry>
        <mesh filename="package://robot_boat/meshes/caja.STL"/>
      </geometry>
      <material name="azul_claro">
        <color rgba="0.792156862745098 0.819607843137255 0.933333333333333 1"/>
      </material>
    </visual>
    <collision>
      <geometry>
        <box size="0.15 0.1 0.05"/>
      </geometry>
    </collision>
  </link>

  <!-- PUNTA DELANTERA (cono naranja) -->
  <link name="punta">
    <inertial>
      <origin xyz="0 0 0" rpy="0 0 0" />
      <mass value="0.05" />
      <inertia ixx="0.0001" ixy="0" ixz="0" iyy="0.0001" iyz="0" izz="0.0001" />
    </inertial>
    <visual>
      <geometry>
        <cylinder length="0.05" radius="0.03"/>
      </geometry>
      <material name="naranja">
        <color rgba="1 0.549019607843137 0 1"/>
      </material>
    </visual>
    <collision>
      <geometry>
        <cylinder length="0.05" radius="0.03"/>
      </geometry>
    </collision>
  </link>

  <joint name="punta_joint" type="fixed">
    <origin xyz="0.08 0 0" rpy="0 0 0" />
    <parent link="base"/>
    <child link="punta"/>
  </joint>

  <!-- MOTOR IZQUIERDO -->
  <link name="motor_left">
    <inertial>
      <origin xyz="0 0 0" rpy="0 0 0" />
      <mass value="0.05" />
      <inertia ixx="0.0001" ixy="0" ixz="0" iyy="0.0001" iyz="0" izz="0.0001" />
    </inertial>
    <visual>
      <geometry>
        <cylinder length="0.08" radius="0.015"/>
      </geometry>
      <material name="gris_claro">
        <color rgba="0.796078431372549 0.823529411764706 0.937254901960784 1"/>
      </material>
    </visual>
    <collision>
      <geometry>
        <cylinder length="0.08" radius="0.015"/>
      </geometry>
    </collision>
  </link>

  <joint name="motor_left_joint" type="continuous">
    <origin xyz="-0.04 -0.08 0" rpy="0 1.5708 0" />
    <parent link="base"/>
    <child link="motor_left"/>
    <axis xyz="1 0 0"/>
    <limit effort="10.0" velocity="10.0"/>
    <dynamics damping="0.1" friction="0.05"/>
  </joint>

  <!-- MOTOR DERECHO -->
  <link name="motor_right">
    <inertial>
      <origin xyz="0 0 0" rpy="0 0 0" />
      <mass value="0.05" />
      <inertia ixx="0.0001" ixy="0" ixz="0" iyy="0.0001" iyz="0" izz="0.0001" />
    </inertial>
    <visual>
      <geometry>
        <cylinder length="0.08" radius="0.015"/>
      </geometry>
      <material name="gris_claro">
        <color rgba="0.796078431372549 0.823529411764706 0.937254901960784 1"/>
      </material>
    </visual>
    <collision>
      <geometry>
        <cylinder length="0.08" radius="0.015"/>
      </geometry>
    </collision>
  </link>

  <joint name="motor_right_joint" type="continuous">
    <origin xyz="0.04 -0.08 0" rpy="0 1.5708 0" />
    <parent link="base"/>
    <child link="motor_right"/>
    <axis xyz="1 0 0"/>
    <limit effort="10.0" velocity="10.0"/>
    <dynamics damping="0.1" friction="0.05"/>
  </joint>

</robot>

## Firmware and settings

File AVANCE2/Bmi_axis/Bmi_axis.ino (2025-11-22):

#include <DFRobot_BMI160.h>

DFRobot_BMI160 bmi160;

// Variables para valores tipo joystick
int joystickX = 0;  // Izquierda/Derecha (-100 a 100)
int joystickY = 0;  // Adelante/Atrás (-100 a 100)

// Zona muerta para evitar drift
const int DEADZONE = 15;

// Umbrales para mapear giroscopio a valores de joystick
const int GYRO_MIN = 100;   // Movimiento mínimo para empezar a contar
const int GYRO_MAX = 1000;  // Movimiento máximo (se mapea a 100%)

// Filtro de suavizado
const float ALPHA = 0.6;
float filteredX = 0;
float filteredY = 0;

// Decay para volver a centro cuando no hay movimiento
const float DECAY_RATE = 0.85;  // Qué tan rápido vuelve a centro

void setup(){
  Serial.begin(115200);
  
  // Intentar inicializar
  if (bmi160.I2cInit(0x69) != BMI160_OK && bmi160.I2cInit(0x68) != BMI160_OK){
    while(1);  // Si falla, detener
  }
  
  delay(1000);
}

void loop(){
  int rslt;
  int16_t accelGyro[6]={0}; 
  
  // Leer datos del sensor
  rslt = bmi160.getAccelGyroData(accelGyro);
  
  if(rslt == 0){
    // Giroscopio
    int16_t gx = accelGyro[3];  // Roll (izquierda/derecha)
    int16_t gy = accelGyro[4];  // Pitch (adelante/atrás)
    
    // Mapear valores de giroscopio a rango -100 a 100
    int rawX = 0;
    int rawY = 0;
    
    // Eje X (izquierda/derecha)
    if (abs(gx) > GYRO_MIN) {
      rawX = map(constrain(gx, -GYRO_MAX, GYRO_MAX), -GYRO_MAX, GYRO_MAX, -100, 100);
    }
    
    // Eje Y (adelante/atrás) - invertido porque gy negativo es adelante
    if (abs(gy) > GYRO_MIN) {
      rawY = map(constrain(gy, -GYRO_MAX, GYRO_MAX), -GYRO_MAX, GYRO_MAX, -100, 100);
      rawY = -rawY;  // Invertir para que adelante sea positivo
    }
    
    // Aplicar filtro de suavizado
    filteredX = ALPHA * filteredX + (1 - ALPHA) * rawX;
    filteredY = ALPHA * filteredY + (1 - ALPHA) * rawY;
    
    // Aplicar decay (volver a centro gradualmente)
    if (abs(gx) < GYRO_MIN) {
      filteredX *= DECAY_RATE;
    }
    if (abs(gy) < GYRO_MIN) {
      filteredY *= DECAY_RATE;
    }
    
    // Convertir a enteros
    joystickX = (int)filteredX;
    joystickY = (int)filteredY;
    
    // Aplicar zona muerta
    if (abs(joystickX) < DEADZONE) joystickX = 0;
    if (abs(joystickY) < DEADZONE) joystickY = 0;
    
    // Limitar rango
    joystickX = constrain(joystickX, -100, 100);
    joystickY = constrain(joystickY, -100, 100);
    
    // Enviar datos en formato para ROS
    // Formato: X:valor,Y:valor
    Serial.print("X:");
    Serial.print(joystickX);
    Serial.print(",Y:");
    Serial.println(joystickY);
  }
  
  delay(50);  // 20Hz
}

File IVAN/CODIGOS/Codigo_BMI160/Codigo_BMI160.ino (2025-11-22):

#include <DFRobot_BMI160.h>

DFRobot_BMI160 bmi160;
const int8_t i2c_addr = 0x69;

void setup() {
  Serial.begin(115200);
  delay(2000);
  
  Serial.println("=================================");
  Serial.println("  BMI160 - TEST DE DIAGNOSTICO");
  Serial.println("=================================");
  Serial.println();
  
  // Reset del sensor
  if (bmi160.softReset() != BMI160_OK){
    Serial.println(" ERROR: softReset falló");
    while(1);
  } else {
    Serial.println(" softReset OK");
  }
  
  delay(100);
  
  // Inicializar I2C
  if (bmi160.I2cInit(i2c_addr) != BMI160_OK){
    Serial.println(" ERROR: I2cInit falló");
    Serial.println("   Revisa las conexiones I2C:");
    Serial.println("   SDA → A4");
    Serial.println("   SCL → A5");
    Serial.println("   VCC → 3.3V o 5V");
    Serial.println("   GND → GND");
    while(1);
  } else {
    Serial.println(" I2cInit OK");
  }
  
  Serial.println();
  Serial.println("Mueve el sensor para ver cambios");
  Serial.println("Si los valores NO cambian = problema de hardware");
  Serial.println();
  Serial.println("GyroX\tGyroY\tGyroZ\tAccX\tAccY\tAccZ");
}

void loop() {
  int16_t accelGyro[6] = {0};
  
  // Leer datos del sensor
  int rslt = bmi160.getAccelGyroData(accelGyro);
  
  if (rslt == 0) {
    // IMPRIMIR VALORES CRUDOS (sin filtros)
    // Esto debe cambiar cuando muevas el sensor
    
    // Giroscopio (velocidades angulares)
    Serial.print(accelGyro[0]); Serial.print("\t");
    Serial.print(accelGyro[1]); Serial.print("\t");
    Serial.print(accelGyro[2]); Serial.print("\t");
    
    // Acelerómetro
    Serial.print(accelGyro[3]); Serial.print("\t");
    Serial.print(accelGyro[4]); Serial.print("\t");
    Serial.println(accelGyro[5]);
    
  } else {
    Serial.println(" ERROR: getAccelGyroData falló");
  }
  
  delay(100);  // 10Hz para diagnóstico
}
